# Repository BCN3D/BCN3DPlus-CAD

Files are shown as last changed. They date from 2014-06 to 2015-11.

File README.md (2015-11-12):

CAD
===

Do you want to redesign any part of the printer? Here you have the CAD files. Easy as pie.

BCN3D is commited to the global Open Source Project REPRAP. It means you can download all the source files, even the designs of the mechanical pieces that compose the printer. The objective is to get faster and better feedback from the community using our printers. If you detect any error or have any improvements, please let us know by creating an Issue in the GitHub Repository.

You will find folders for the BCN3D+, the dual extruder and pretty soon other upgrades. In each folder there is a BOM (bill of materials), a complete Assembly and the printed parts.

>The fun thing with the STL files is that you can preview the models directly within the browser.
Check the feature. [STL Visualization](https://github.com/reprapbcn/CAD/blob/master/upperVertex.STL)

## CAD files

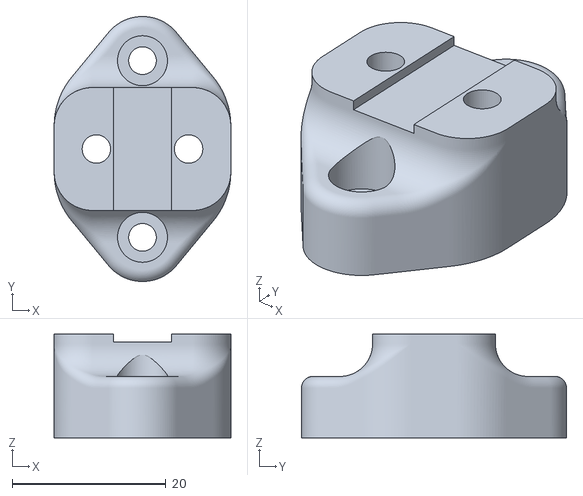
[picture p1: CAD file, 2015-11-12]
BCN3D+/Printed Parts/BCN3D1.2-M03C02.0P02A Belt guide.STL
23.0 x 34.5 x 13.5

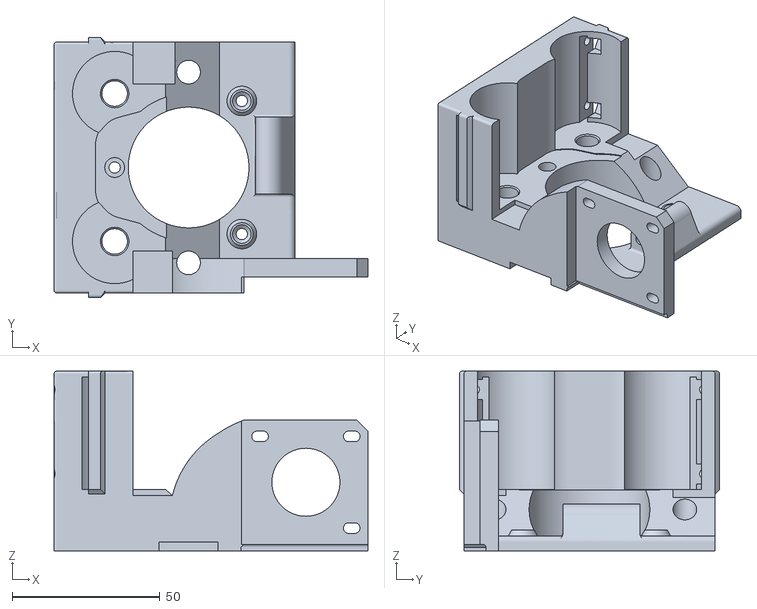
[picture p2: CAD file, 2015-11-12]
PASTE Extruder/Printed parts/BCN3DPaste-M01C00.0P01A Body1.STL
106.2 x 88.0 x 60.8

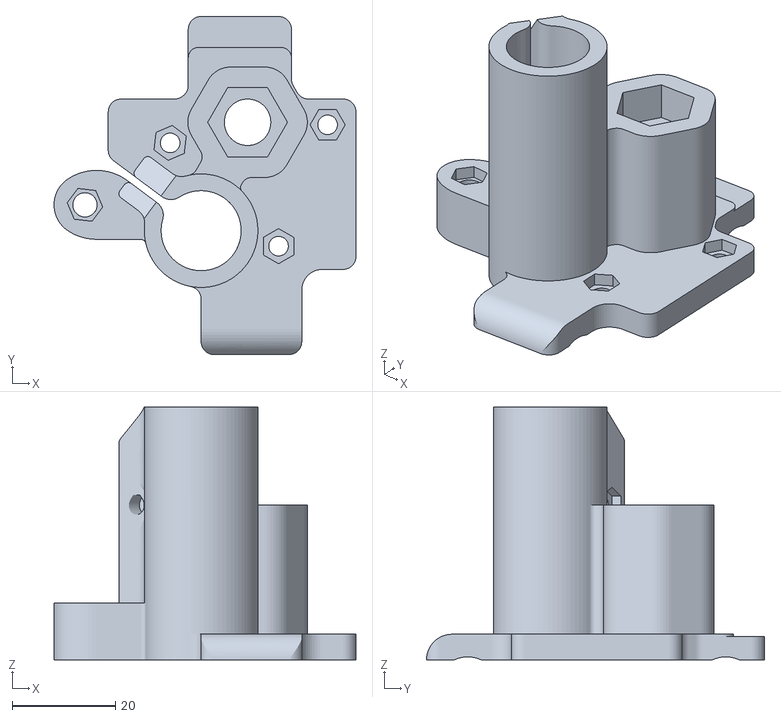
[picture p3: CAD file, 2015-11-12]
BCN3D+/Printed Parts/BCN3D1.2-M02C01.0P02C Z motion motor.STL
58.5 x 65.5 x 49.0

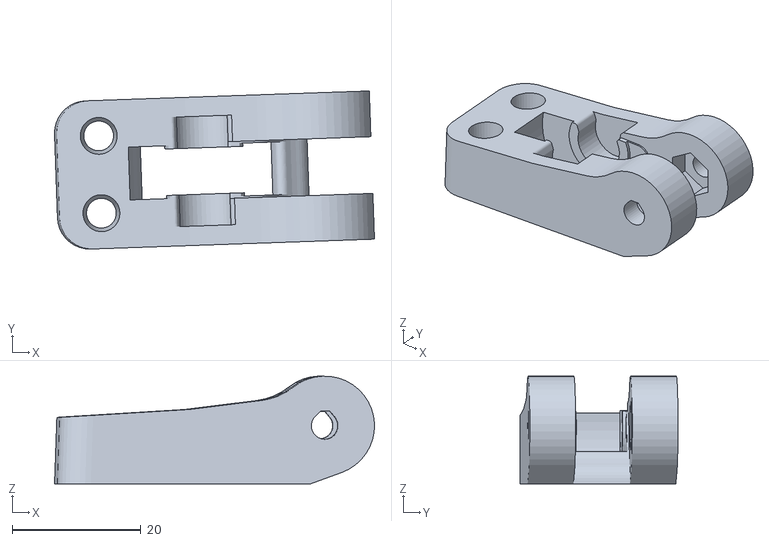
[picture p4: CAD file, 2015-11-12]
Dual Extruder/Printed Parts/BCN3D1.2-M05C01.0P04C Extruder idler (x2).STL
49.6 x 24.5 x 16.7

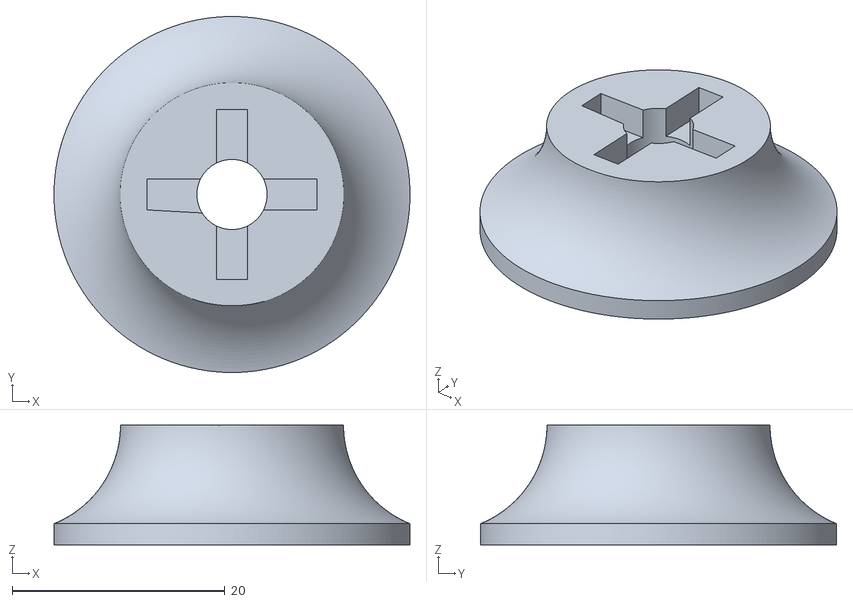
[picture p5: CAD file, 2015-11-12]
PASTE Extruder/Printed parts/BCN3DPaste-M01C00.0P06A Plunger 2.STL
33.5 x 33.5 x 11.3

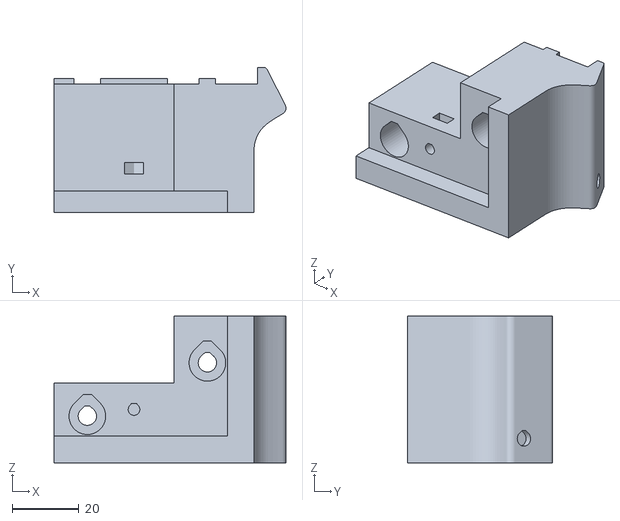
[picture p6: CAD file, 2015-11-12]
BCN3D+/Printed Parts/BCN3D1.2-M01C00.0P10C Screen leg.STL
69.6 x 43.5 x 44.0

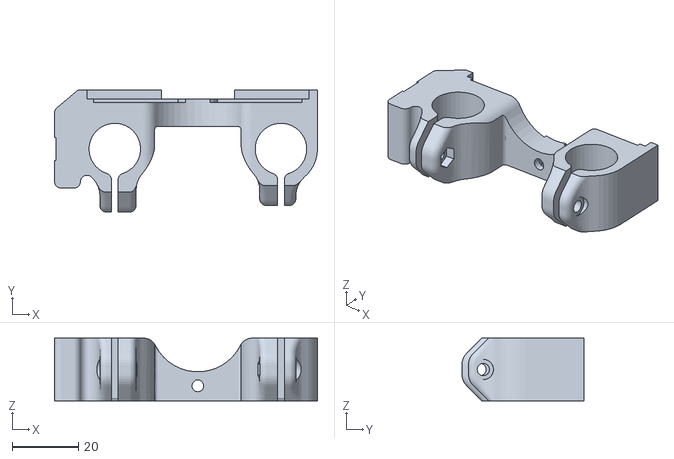
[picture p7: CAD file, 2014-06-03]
Dual Extruder/Printed Parts/BCN3D1.2-M02C02.0P02C Right carriage.STL
79.2 x 36.8 x 18.9

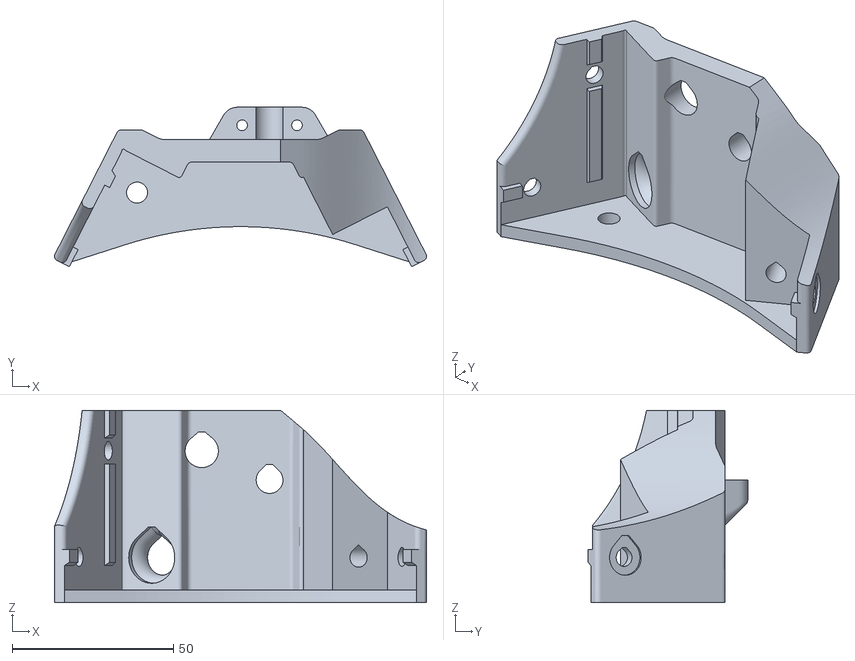
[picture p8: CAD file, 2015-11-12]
PASTE Extruder/Printed parts/BCN3DPaste-M01C00.0P21A Upper vertex right.STL
115.2 x 49.4 x 59.6

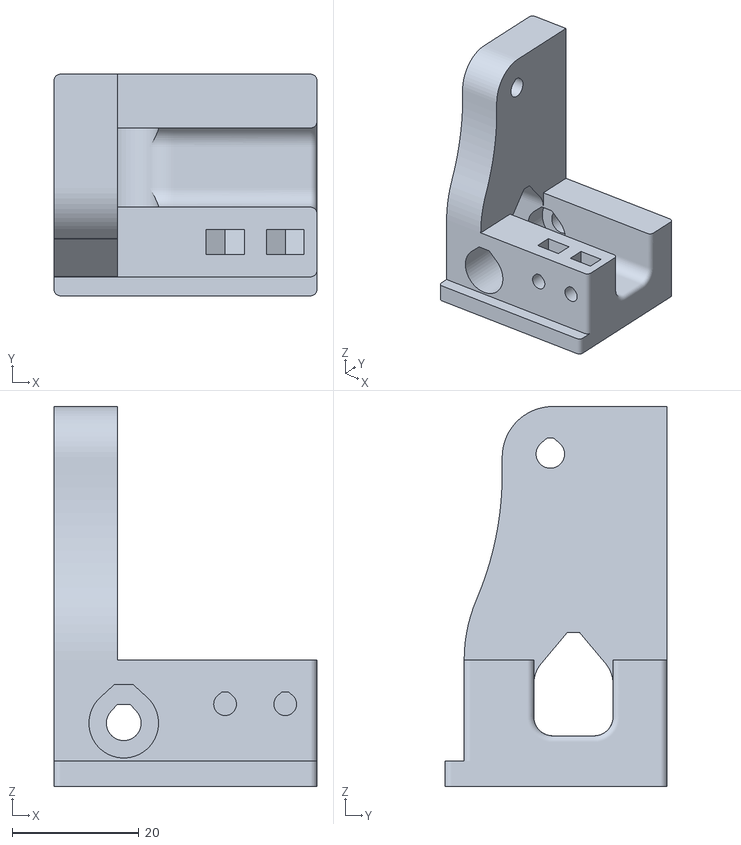
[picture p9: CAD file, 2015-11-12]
BCN3D+/Printed Parts/BCN3D1.2-M07C00.0P02C Rear Source Holder.STL
41.5 x 35.0 x 60.0

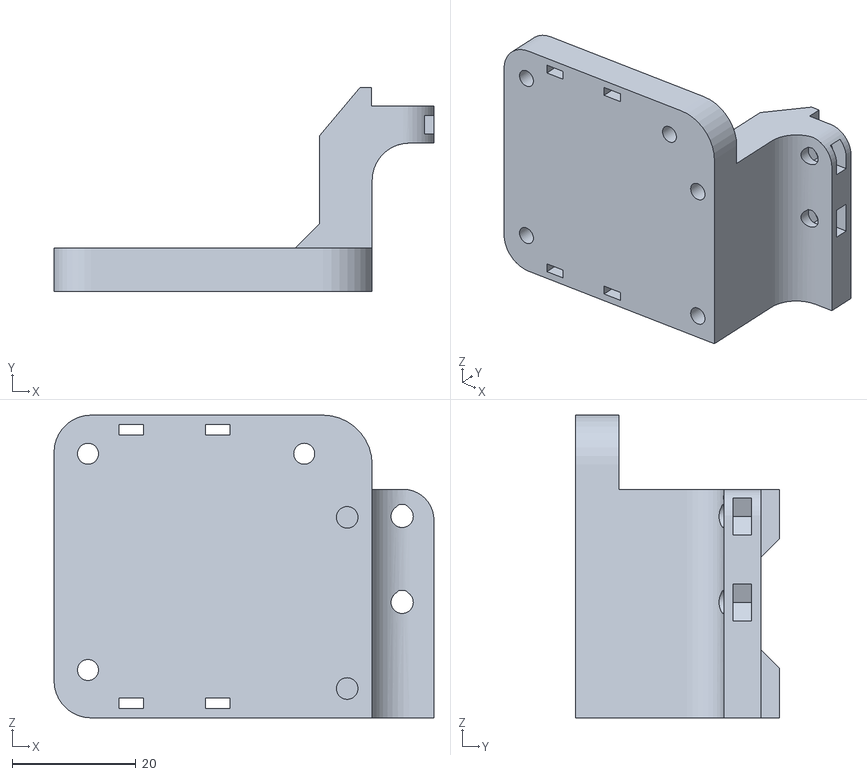
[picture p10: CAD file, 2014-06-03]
Dual Extruder/Printed Parts/BCN3D1.2-M05C03.0P01E Layer fan support.STL
61.5 x 33.0 x 49.0

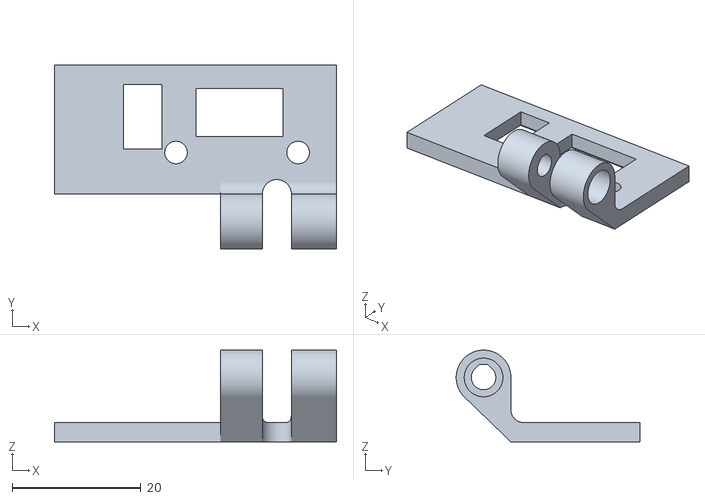
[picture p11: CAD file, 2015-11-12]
PASTE Extruder/Printed parts/BCN3DPaste-M01C00.0P18A Z EndstopFeature 1.STL
43.7 x 28.5 x 14.2

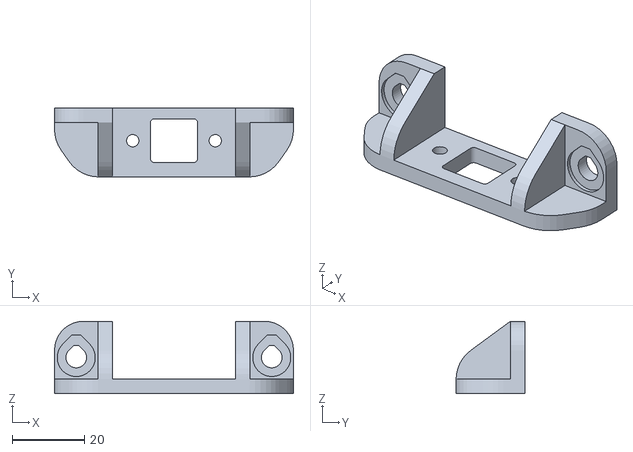
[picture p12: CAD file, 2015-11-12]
BCN3D+/Printed Parts/BCN3D1.2-M01C00.0P12C USB holder.STL
66.0 x 19.0 x 20.0

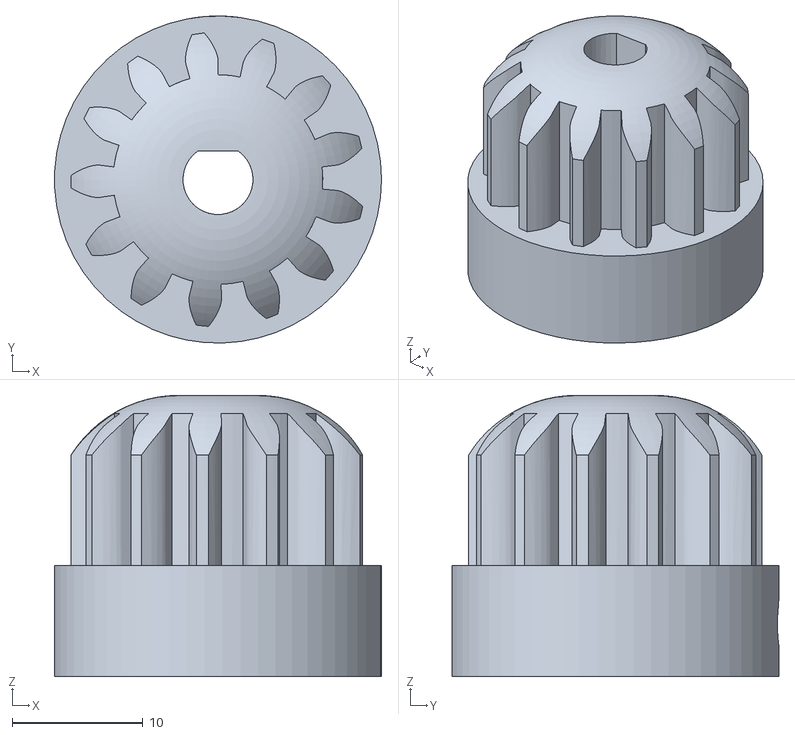
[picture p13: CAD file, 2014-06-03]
Dual Extruder/Printed Parts/BCN3D1.2-M05C01.0P03B Small gear (x2).STL
25.0 x 25.0 x 21.5

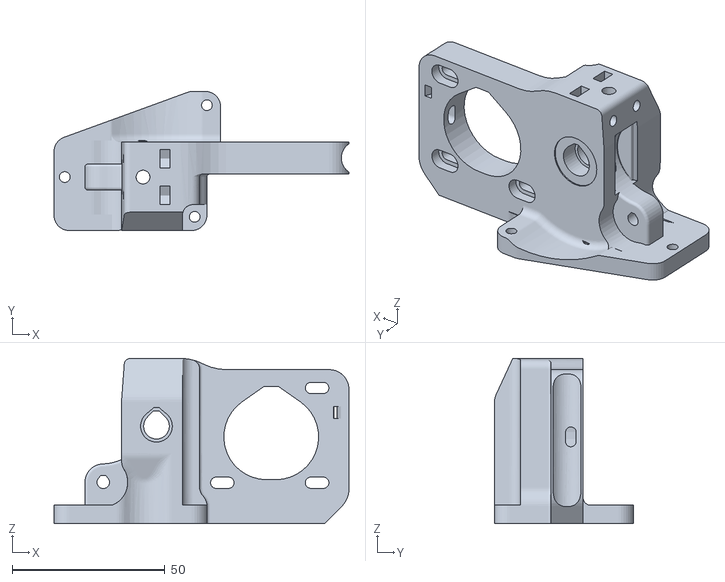
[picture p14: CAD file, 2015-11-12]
BCN3D+/Printed Parts/BCN3D1.2-M05C01.0P01J Extruder body right.STL
96.5 x 45.5 x 54.0

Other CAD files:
PASTE Extruder/Printed parts/BCN3DPaste-M01C00.0P22A Upper vertex left.STL
PASTE Extruder/Printed parts/BCN3DPaste-M01C00.0P04A Link right.STL
BCN3D+/Printed Parts/BCN3D1.2-M03C01.0P01C Stepper Mount.STL
Dual Extruder/Printed Parts/BCN3D1.2-M05C01.0P02C Large gear (x2).STL
BCN3D+/Printed Parts/BCN3D1.2-M01C00.0P05C Lower vertex right.STL
BCN3D+/Printed Parts/BCN3D1.2-M01C00.0P06C Lower vertex left.STL
BCN3D+/Printed Parts/BCN3D1.2-M01C00.0P07B Upper vertex.STL
BCN3D+/Printed Parts/BCN3D1.2-M01C00.0P08A Z bar clamp.STL
BCN3D+/Printed Parts/BCN3D1.2-M01C00.0P09C Leg.STL
BCN3D+/Printed Parts/BCN3D1.2-M01C00.0P21A Bottom cover holder back.STL
BCN3D+/Printed Parts/BCN3D1.2-M01C00.0P24C Power plug leg.STL
BCN3D+/Printed Parts/BCN3D1.2-M01C00.0P25A Power switch leg 2.STL
BCN3D+/Printed Parts/BCN3D1.2-M02C01.0P01A X-end motor.STL
BCN3D+/Printed Parts/BCN3D1.2-M02C01.0P03B X-end idler.STL
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

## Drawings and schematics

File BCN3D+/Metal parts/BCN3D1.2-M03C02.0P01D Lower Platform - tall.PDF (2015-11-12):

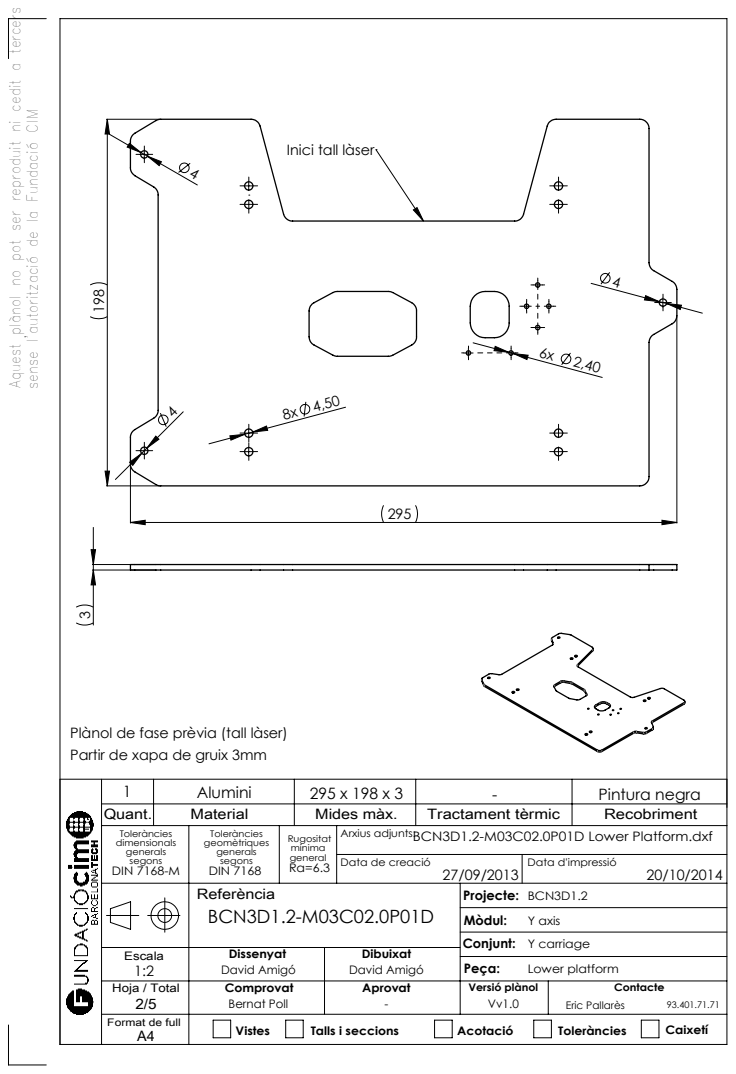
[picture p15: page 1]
Mides màx.; Tractament tèrmic; Recobriment; Data de creació; Data d'impressió; Vistes; Talls i seccions; Acotació; Toleràncies; Caixetí; Lower platform; - Pintura negra

Aquest plànol no pot ser reproduit ni cedit a tercers

sense l'autorització de la Fundació CIM

Inici tall làser

Plànol de fase prèvia (tall làser)
Partir de xapa de gruix 3mm
Quant.

Toleràncies dimensionals generals segons DIN 7168-M | Toleràncies geomètriques generals segons DIN 7168 | Rugositat mínima general Ra=6.3 | Arxius adjunts: BCN3D1.2-M03C02.0P01D Lower Platform.dxf

Referència BCN3D1.2-M03C02.0P01D | Projecte: BCN3D1.2 Mòdul: Y axis Conjunt: Y carriage

Escala 1:2 | Dissenyat David Amigó | Dibuixat David Amigó

Hoja / Total 2/5 | Comprovat Bernat Poll | Aprovat - | Versió plànol Vv1.0 | Contacte Eric Pallarès 93.401.71.71

Format de full A4

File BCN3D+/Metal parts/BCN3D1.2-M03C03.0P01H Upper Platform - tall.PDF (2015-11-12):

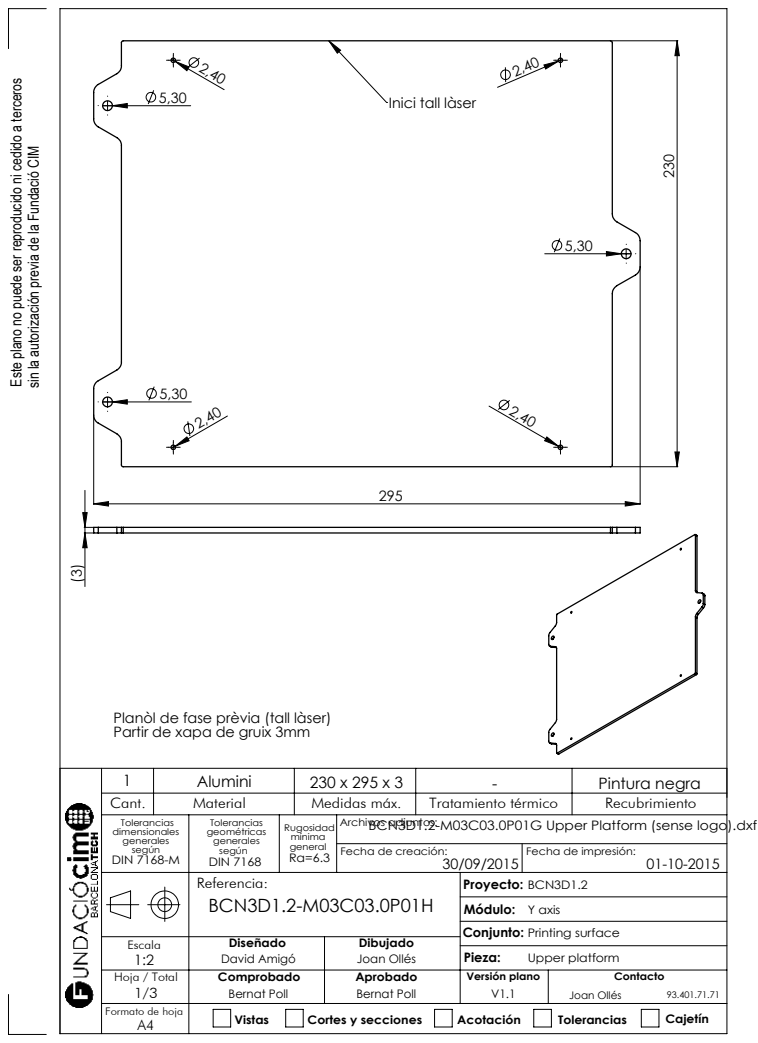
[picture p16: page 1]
Medidas máx.; Tratamiento térmico; Recubrimiento; Fecha de creación:; Fecha de impresión:; Vistas; Cortes y secciones; Acotación; Tolerancias; Cajetín; Upper platform; Pintura negra

Este plano no puede ser reproducido ni cedido a terceros

Inici tall làser

sin la autorización previa de la Fundació CIM

Planòl de fase prèvia (tall làser)
Partir de xapa de gruix 3mm

Tolerancias dimensionales generales según DIN 7168-M | Tolerancias geométricas generales según DIN 7168 | Rugosidad mínima general Ra=6.3 | Archivos adjuntos:

BCN3D1.2-M03C03.0P01G Upper Platform (sense logo).dxf

Referencia: BCN3D1.2-M03C03.0P01H | Proyecto: BCN3D1.2 Módulo: Y axis Conjunto: Escala Printing surface

1:2 | Diseñado David Amigó | Dibujado Joan Ollés

Hoja / Total 1/3 | Comprobado Bernat Poll | Aprobado Bernat Poll | Versión plano V1.1 | Contacto Joan Ollés 93.401.71.71

Formato de hoja A4

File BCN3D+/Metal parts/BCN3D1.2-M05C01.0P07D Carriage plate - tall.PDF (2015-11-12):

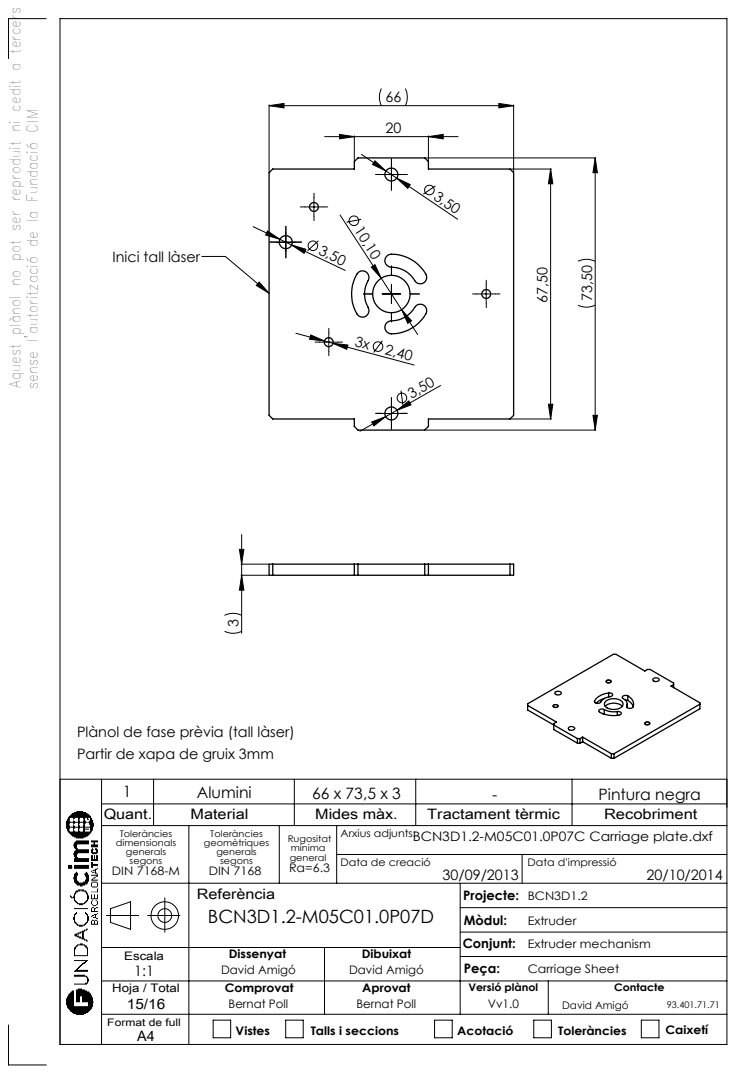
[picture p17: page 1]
Mides màx.; Tractament tèrmic; Recobriment; Data de creació; Data d'impressió; Vistes; Talls i seccions; Acotació; Toleràncies; Caixetí; Carriage Sheet; - Pintura negra

Aquest plànol no pot ser reproduit ni cedit a tercers

sense l'autorització de la Fundació CIM

Inici tall làser

Plànol de fase prèvia (tall làser)
Partir de xapa de gruix 3mm
Quant.

Toleràncies dimensionals generals segons DIN 7168-M | Toleràncies geomètriques generals segons DIN 7168 | Rugositat mínima general Ra=6.3 | Arxius adjunts: BCN3D1.2-M05C01.0P07C Carriage plate.dxf

Referència BCN3D1.2-M05C01.0P07D | Projecte: BCN3D1.2 Mòdul: Extruder Conjunt: Extruder mechanism

Escala 1:1 | Dissenyat David Amigó | Dibuixat David Amigó

Hoja / Total 15/16 | Comprovat Bernat Poll | Aprovat Bernat Poll | Versió plànol Vv1.0 | Contacte David Amigó 93.401.71.71

Format de full A4

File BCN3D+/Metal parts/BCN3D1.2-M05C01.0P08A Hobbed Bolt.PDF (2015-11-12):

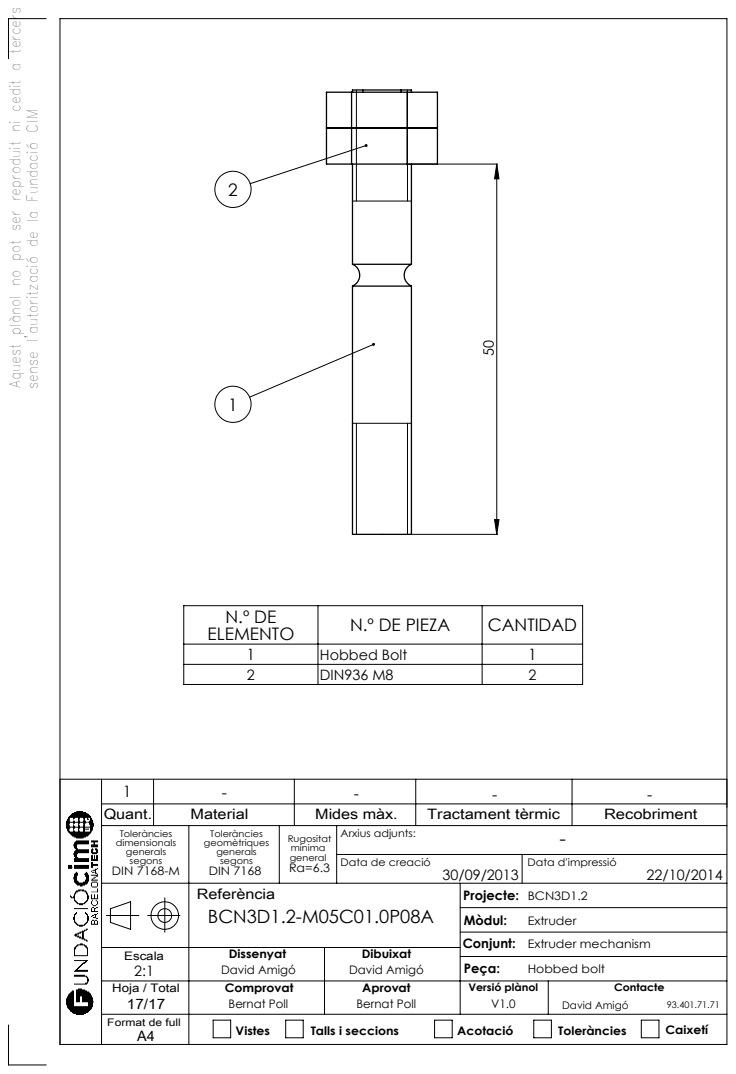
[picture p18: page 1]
Mides màx.; Tractament tèrmic; Recobriment; Data de creació; Data d'impressió; Vistes; Talls i seccions; Acotació; Toleràncies; Caixetí; Hobbed bolt; ELEMENTO; N.º DE PIEZA; CANTIDAD 1; Hobbed Bolt; DIN936 M8

Aquest plànol no pot ser reproduit ni cedit a tercers

sense l'autorització de la Fundació CIM

Toleràncies dimensionals generals segons DIN 7168-M | BCN3D1.2-M05C01.0P08A -Toleràncies geomètriques generals segons DIN 7168 | Rugositat mínima general Ra=6.3 | Arxius adjunts: | -

Referència | Projecte: BCN3D1.2 Mòdul: Extruder Conjunt: Extruder mechanism

Escala 2:1 | Dissenyat David Amigó | Dibuixat David Amigó

Hoja / Total 17/17 | Comprovat Bernat Poll | Aprovat Bernat Poll | Versió plànol V1.0 | Contacte David Amigó 93.401.71.71

Format de full A4

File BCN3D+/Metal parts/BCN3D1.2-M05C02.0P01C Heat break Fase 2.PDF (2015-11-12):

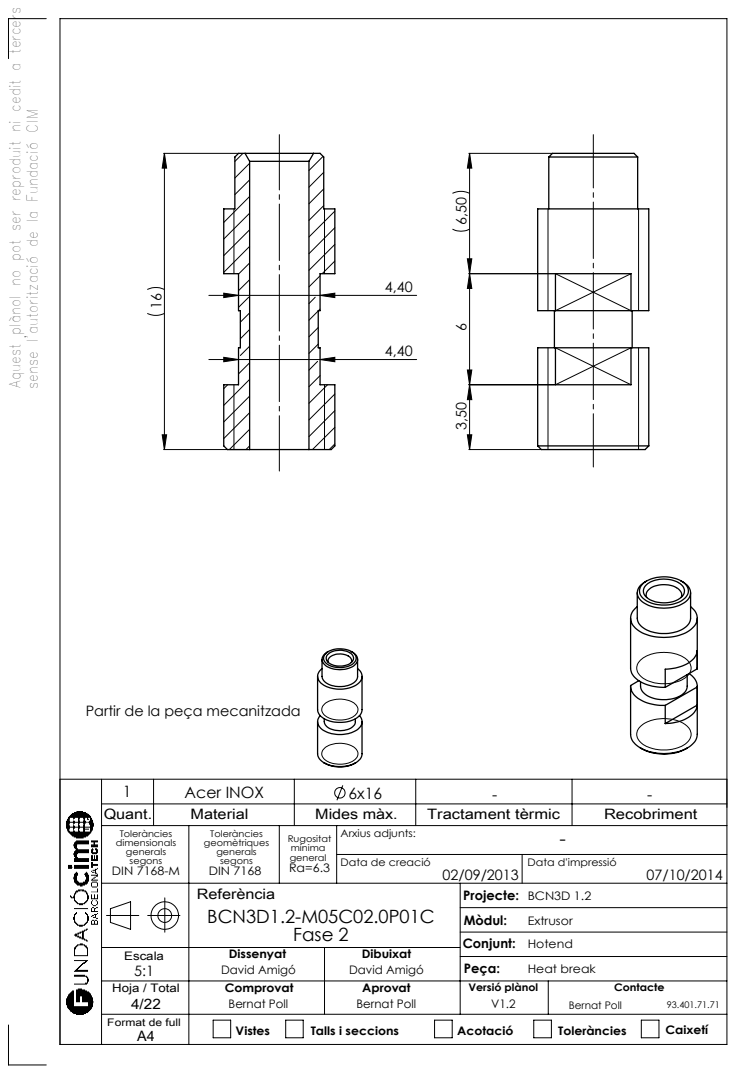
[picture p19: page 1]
Mides màx.; Tractament tèrmic; Recobriment; Data de creació; Data d'impressió; Vistes; Talls i seccions; Acotació; Toleràncies; Caixetí; Acer INOX; Heat break

Aquest plànol no pot ser reproduit ni cedit a tercers

sense l'autorització de la Fundació CIM

Partir de la peça mecanitzada

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

Referència BCN3D1.2-M05C02.0P01C Fase 2 | Projecte: BCN3D 1.2 Mòdul: Extrusor Conjunt: Hotend

Escala 5:1 | Dissenyat David Amigó | Dibuixat David Amigó

Hoja / Total 4/22 | Comprovat Bernat Poll | Aprovat Bernat Poll | Versió plànol V1.2 | Contacte Bernat Poll 93.401.71.71

Format de full A4

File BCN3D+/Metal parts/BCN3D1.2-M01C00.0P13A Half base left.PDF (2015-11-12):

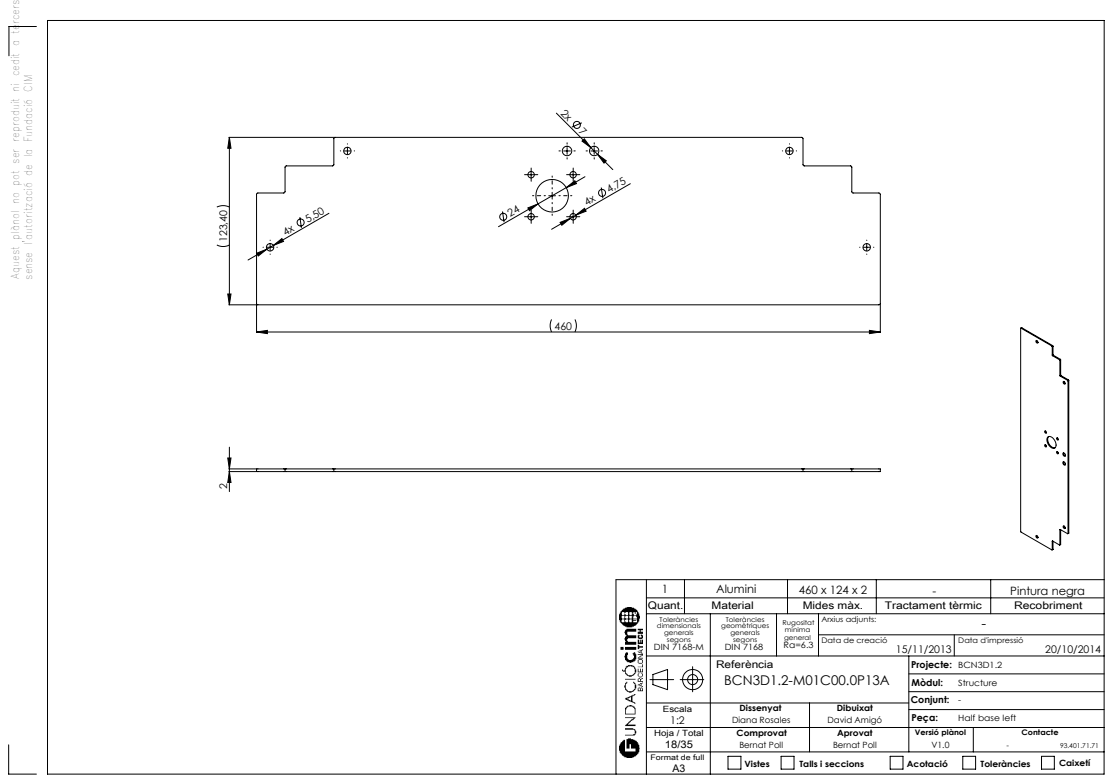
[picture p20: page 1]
Mides màx.; Tractament tèrmic; Recobriment; Data de creació; Data d'impressió; Vistes; Talls i seccions; Acotació; Toleràncies; Caixetí; - Pintura negra

Aquest plànol no pot ser reproduit ni cedit a tercers

sense l'autorització de la Fundació CIM

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

Referència BCN3D1.2-M01C00.0P13A | Projecte: BCN3D1.2 Mòdul: Structure -Conjunt:

Escala 1:2 | Dissenyat Diana Rosales | Dibuixat David Amigó

Half base left

Hoja / Total 18/35 | Comprovat Bernat Poll | Aprovat Bernat Poll | Versió plànol V1.0 | Contacte -93.401.71.71

Format de full A3

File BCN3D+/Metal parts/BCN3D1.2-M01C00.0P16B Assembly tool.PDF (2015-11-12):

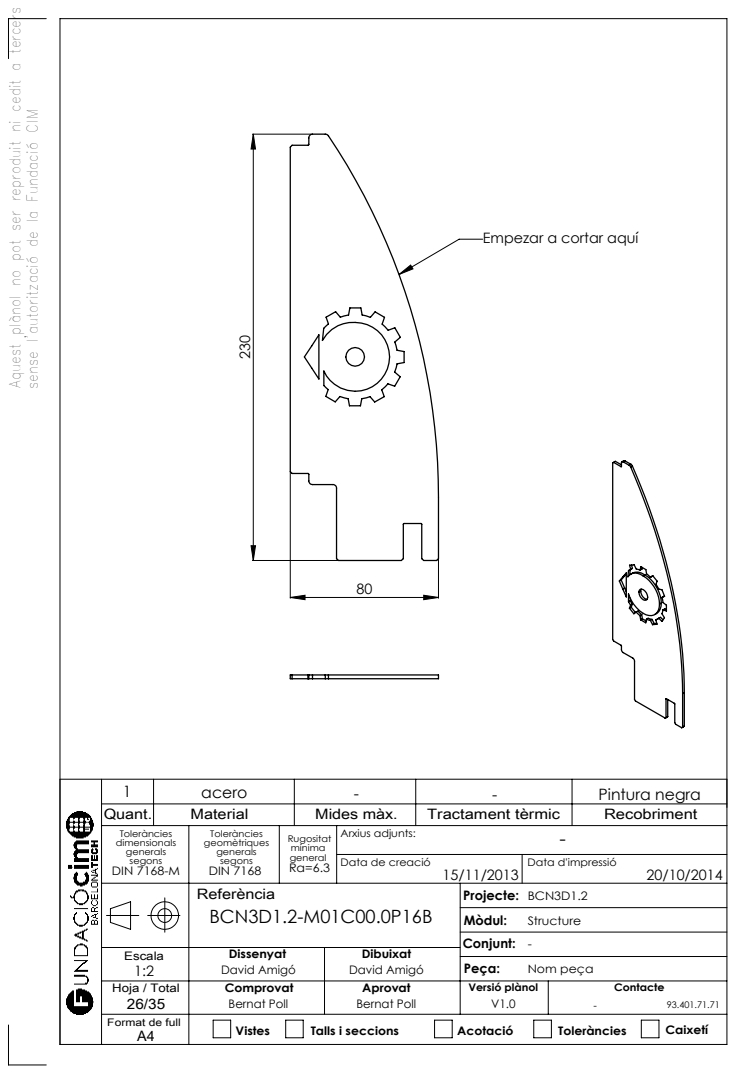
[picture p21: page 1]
Mides màx.; Tractament tèrmic; Recobriment; Data de creació; Data d'impressió; Vistes; Talls i seccions; Acotació; Toleràncies; Caixetí; Nom peça; - Pintura negra

Aquest plànol no pot ser reproduit ni cedit a tercers

sense l'autorització de la Fundació CIM

Empezar a cortar aquí

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

Referència BCN3D1.2-M01C00.0P16B | Projecte: BCN3D1.2 Mòdul: Structure -Conjunt:

Escala 1:2 | Dissenyat David Amigó | Dibuixat David Amigó

Hoja / Total 26/35 | Comprovat Bernat Poll | Aprovat Bernat Poll | Versió plànol V1.0 | Contacte -93.401.71.71

Format de full A4

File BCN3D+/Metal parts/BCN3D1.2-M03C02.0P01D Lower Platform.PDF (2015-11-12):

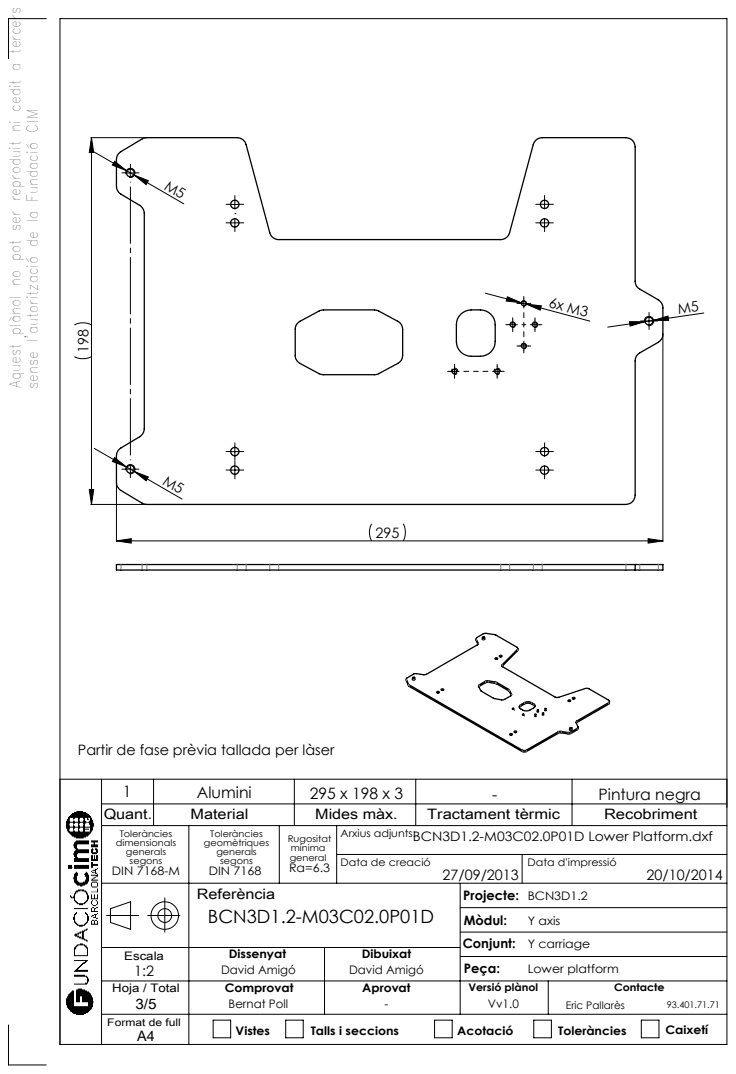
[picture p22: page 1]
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

Aquest plànol no pot ser reproduit ni cedit a tercers
- Pintura negra 6x M3

sense l'autorització de la Fundació CIM

Partir de fase prèvia tallada per làser
Quant.

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

Referència BCN3D1.2-M03C02.0P01D | Projecte: BCN3D1.2 Mòdul: Y axis Conjunt: Y carriage

Escala 1:2 | Dissenyat David Amigó | Dibuixat David Amigó

Hoja / Total 3/5 | Comprovat Bernat Poll | Aprovat - | Versió plànol Vv1.0 | Contacte Eric Pallarès 93.401.71.71

Format de full A4

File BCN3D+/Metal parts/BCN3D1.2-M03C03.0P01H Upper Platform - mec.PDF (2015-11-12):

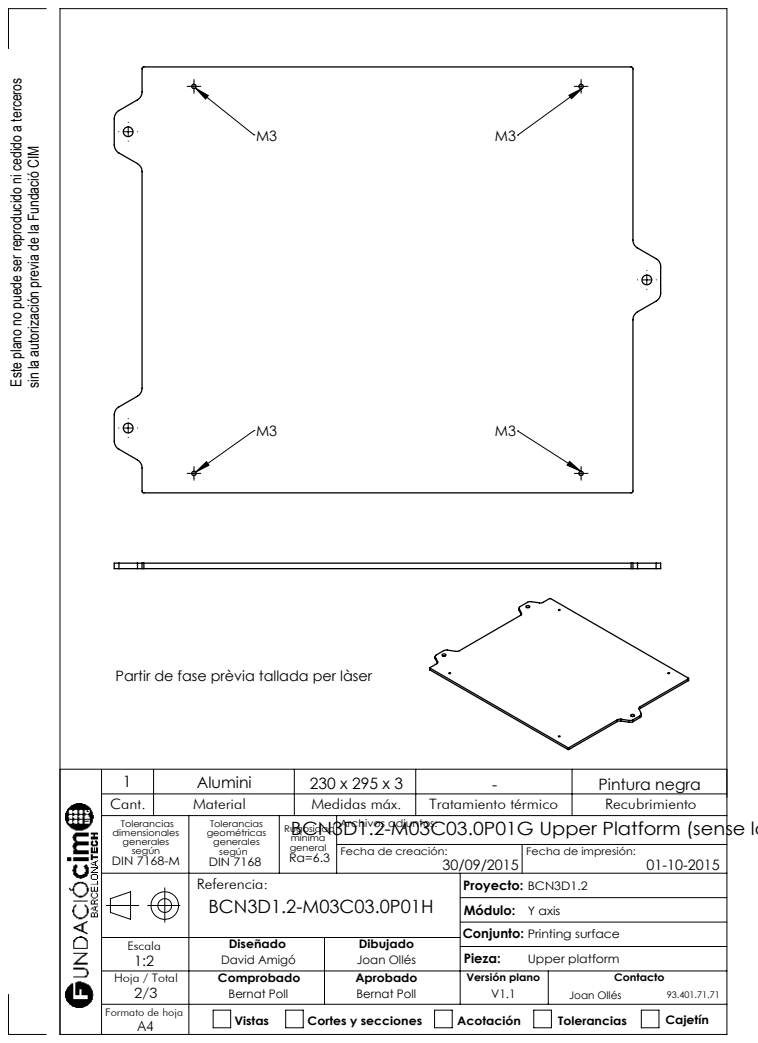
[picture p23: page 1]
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

Este plano no puede ser reproducido ni cedido a terceros

sin la autorización previa de la Fundació CIM

Partir de fase prèvia tallada per làser

Medidas máx.
BCN3D1.2-M03C03.0P01G Upper Platform (sense logo).dxf

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

Referencia: BCN3D1.2-M03C03.0P01H | Proyecto: BCN3D1.2 Módulo: Y axis Conjunto: Escala Printing surface

1:2 | Diseñado David Amigó | Dibujado Joan Ollés

Hoja / Total 2/3 | Comprobado Bernat Poll | Aprobado Bernat Poll | Versión plano V1.1 | Contacto Joan Ollés 93.401.71.71

Formato de hoja A4

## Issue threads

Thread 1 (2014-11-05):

Small Gear

mcanet, 2014-11-05:
The small gear the shaft it is a little moving with Nema17 and in my printer after few prints this piece stop functioning since turn inside shaft. I think should be 5% smaller to be totally fix on the place and resist better higher tensions. I did try just to scale 5% and works the shaft although it is not a functional piece since gear teeth gets too small: https://github.com/reprapbcn/CAD/blob/master/BCN3D%2B/Printed%20Parts/STL/BCN3D1.2-M05C01.0P03A%20Small%20gear.STL

Closed 2015-01-08.

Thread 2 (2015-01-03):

STL not up to date

Juju2707, 2015-01-03:
Hello,

Can you update STL like they are in the BOM folder (for example Extruder Body are not the same).

Regards

kitusmark, 2015-01-08:
Hi @Juju2707. We're working on updating all the dependencies as we are updating our servers.

In a few days this should be fixed. Thanks!

Closed 2015-10-28.

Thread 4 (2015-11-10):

Aquesta peça hauría de estar dentada.

rskproductions, 2015-11-10:
Aquesta STL es diferent. No te dens, com la definida a BCN3D1.2-M02C02.0P03B Belt clamp
Salut.

kitusmark, 2015-11-12:
S'ha actualitzat tot el repositori. Ara hauría de sortir bé.

Gracies per la informació.

Closed 2015-11-12.

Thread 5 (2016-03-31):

Faulty STL files

temetee, 2016-03-31:
Hi, I tried to print the left carriage part for BCN3D+ and I couldnt open it on any software (solidworks, slic3r,netfabb...) Could you please investigate what is wrong with the file?

rskproductions, 2016-03-31:
I believe this STL is not a source. But there are the source any directory.
BS.

temetee, 2016-03-31:
Okay, didn't know how the site works. STLs are fine now.

rskproductions, 2016-03-31:
Right

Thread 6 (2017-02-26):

Missing left Y carriage in whole machine .STEP file

ankou29666, 2017-02-26:

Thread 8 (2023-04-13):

Mitllorar peces BCN3D+

rskproductions, 2023-04-13:
Ya no estan els fitxers de Solidworks. Imposible fer mitllores sense l'original .

terabyte11, 2023-04-14:
Hola RSK estan les peces en format .STEP que es poden modificar com a un solid unic.

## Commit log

2014-05-22 Added all the STL files of the BCN3D+
    [BCN3D1.2-M01C00.0P05C Lower vertex right.STL, BCN3D1.2-M01C00.0P06C Lower vertex left.STL, BCN3D1.2-M01C00.0P07A Upper vertex.STL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]
2014-06-03 Update
    New organization of the folder's scheme
    [BCN3D1.2-M01C00.0P05C Lower vertex right.STL, BCN3D1.2-M01C00.0P06C Lower vertex left.STL, BCN3D1.2-M01C00.0P07A Upper vertex.STL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]
2014-06-04 BOM
    Added all the PDF's from the bill of materials
2014-06-04 github preview file
    Added a STL file as an example to preview right in the downloads page.
    [upperVertex.STL]
2015-11-12 Files Update
    The files have been updated to the latest version, bc3d+, dual and paste
    [BCN3D1.2-M01C00.0P05C Lower vertex right.STL, BCN3D1.2-M01C00.0P06C Lower vertex left.STL, BCN3D1.2-M01C00.0P07A Upper vertex.STL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]
2015-11-12 CAD in STEP format
    Upload the CAD of the BC3D+, dual and paste in STEP format
